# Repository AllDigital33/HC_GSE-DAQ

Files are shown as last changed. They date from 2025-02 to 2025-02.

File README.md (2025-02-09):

# HalfCat Custom GSE and DAQ

See attached overview PDF for details

WHY BUILD A HALFCAT CUSTOM GSE?  
  
The commercial GSE controller design that is detailed in the HalfCat HCR-5100 Mojave Sphinx guidebook works well. It is battle tested with a combined 50+ static fires and launches. It is infinitely easier and cheaper to setup than building your own GSE Controller or DAQ system. HalfCat has always been optimized for low cost, ease and accessibility, and is a great entry point to learn liquid rocketry. 
  
We built our custom HalfCat GSE and DAQ only because we had built ten previous versions for other liquid rockets. It only required minor edits to our existing PCBs, software, and iPad remote. Also, our overall “RocketTalk” project includes a full featured flight computer talking to our hand-held base, as well as the GSE, so we have one integrated hand-held remote talking across three radios to the pad and the rocket. This allows us to fill, launch, and track the rocket all in one, although the GSE Controller and code is separate and can be isolated, especially when doing static fires or testing not involving flight.
  
That said, if you have an amateur EE and some code junkies on your team and you want your own custom GSE controller or DAQ then our open sourced solution can provide you with some good ideas and a starting point. We intentionally built everything with the amateur maker in mind – including Arduino source code, EasyEDA schematics and PCB design, and Apple iOS Swift code. Building your own GSE controller could also be a fun upgrade for a team that has already built and launched their first Mojave Sphinx. 
  
As an added disclaimer… Our HC GSE Controller was developed/modified over the course of 8-10 weeks to support our Mojave Sphinx build, but it is still very much a WIP. We’ve decided to take a snapshot and share our learnings, so student groups can learn, borrow, or reuse some of our ideas and our sloppy code. 
  
FULLY INTEGRATED WITH HALFCAT MOJAVE SPHINX GSE PLUMBING  
  
It should be noted that we used the exact same servos, valves, plumbing, and fittings as specified in HCR 5100 for the Mojave Sphinx GSE. The only addition in our setup is the custom GSE Controller with radio remote and a permanently mounted pressure transducer on the rocket tank (connected back through the umbilical). 
  
GSE CONTROLLER FEATURES  
  
• Control of two pad servo valves for N2O fill and CO2 purging.  
• Control of rocket N2O and fuel main valves  
• Monitoring/recording of rocket tank PT  
• Monitoring/recording of chamber PT (static fire)  
• Igniter firing and local continuity check  
• Full featured three channel DAQ recorder for static fire analysis (tank PT, chamber PT, load cell)  
• Hazard power safety key  
• Automated process tasks for loading and launching to ensure exact timing  
  
iPAD TOUCH REMOTE FEATURES  
  
• Two tab-based control screens including:  
• Main GSE Screen:  
&nbsp;&nbsp;• Manual valve and igniter control  
&nbsp;&nbsp;• Automated processes (launch and load)  
&nbsp;&nbsp;• DAQ control  
&nbsp;&nbsp;• Arming & Disarming  
• GSE Configuration Screen:  
&nbsp;&nbsp;• Launch/Static fire mode  
&nbsp;&nbsp;• Set servo stops  
&nbsp;&nbsp;• Zero PTs  
&nbsp;&nbsp;• Set PT ranges  
   
TECHNOLOGY SUMMARY  
-------------------------------  
  
GSE Controller
  
• Teensy 4.1 Arm7 Microcontroller  
• SD card for DAQ and command logging  
• Arduino IDE / Single C++ Sketch  
• NiceRF LoRa 611Pro 433Mhz serial TTY radio (or use 900 Mhz)  
• Uses 12.6v Lipo battery  
• ADS1115 four channel 16bit ADC  
• DB9 connectors for rocket umbilical  
• DB9 connectors for pad valves  
• 6 pin avionics connector for chamber PT and load cell amplifier (separate)  
• CPU heatsink strapping for thermal management  
• Custom PCB developed using EasyEDA and printed through JLCPCB  
  
iPad Touch-based Remote  
  
• Standard iPad mini (wifi only)  
• Uses RedSerial cable to interface with NiceRF LoRa radio  
• -or- Custom Bluetooth bridge using an ESP32 connected to a NiceRF LoRa 611Pro 433Mhz serial radio  
• Apple xCode IDE with iOS Swift code  
• 7.2v lipo battery and iPad battery  

DISCLAIMER

The open-source code and hardware designs ("Materials") provided here are related to the development and launching of bipropellant liquid rockets. The authors and contributors of these Materials provide them for educational and informational purposes only. The authors and contributors disclaim all responsibility for any injuries, damages, or losses of any nature whatsoever, whether direct, indirect, punitive, incidental, special, consequential, or any other damages, to persons or property, arising out of or connected with the use, misuse, or inability to use the Materials provided here.

Mike & Preston
Sinnoh Sphinx+ SN05
@RocketTalk33 in the Discord

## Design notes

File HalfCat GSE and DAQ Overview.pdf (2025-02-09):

# HalfCat Custom GSE Controller & DAQ

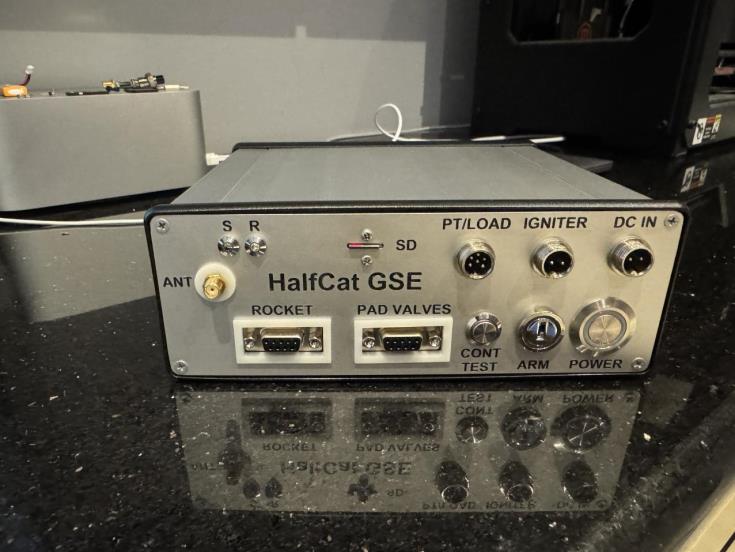
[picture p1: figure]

# Overview and Design

# Version 1.0 – February 2025 Mike & Preston Brinker

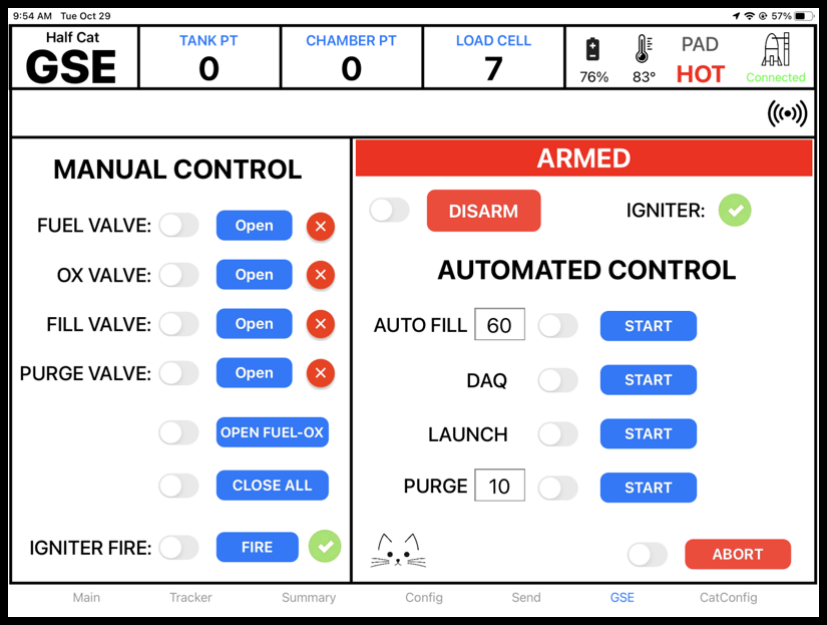
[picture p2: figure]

# Why build a GSE controller for HalfCat Rockets?

The commercial GSE controller design that is detailed in the HalfCat HCR-5100 Mojave Sphinx guidebook works well. It is battle tested with a combined 50+ static fires and launches. It is infinitely easier and cheaper to setup than building your own GSE Controller or DAQ system. HalfCat has always been optimized for low cost, ease and accessibility, and is a great entry point to learn liquid rocketry.

We built our custom HalfCat GSE and DAQ only because we had built ten previous versions for other liquid rockets. It only required minor edits to our existing PCBs, software, and iPad remote. Also, our overall “RocketTalk” project includes a full featured flight computer talking to our hand-held base, as well as the GSE, so we have one integrated hand-held remote talking across three radios to the pad and the rocket. This allows us to fill, launch, and track the rocket all in one, although the GSE Controller and code is separate and can be isolated, especially when doing static fires or testing not involving flight.

That said, if you have an amateur EE and some code junkies on your team and you want your own custom GSE controller or DAQ then our open sourced solution can provide you with some good ideas and a starting point. We intentionally built everything with the amateur maker in mind – including Arduino source code, EasyEDA schematics and PCB design, and Apple iOS Swift code. Building your own GSE controller could also be a fun upgrade for a team that has already built and launched their first Mojave Sphinx.

As an added disclaimer… Our HC GSE Controller was developed/modified over the course of 8-10 weeks to support our Mojave Sphinx build, but it is still very much a WIP. We’ve decided to take a snapshot and share our learnings, so student groups can learn, borrow, or reuse some of our ideas and our sloppy code.

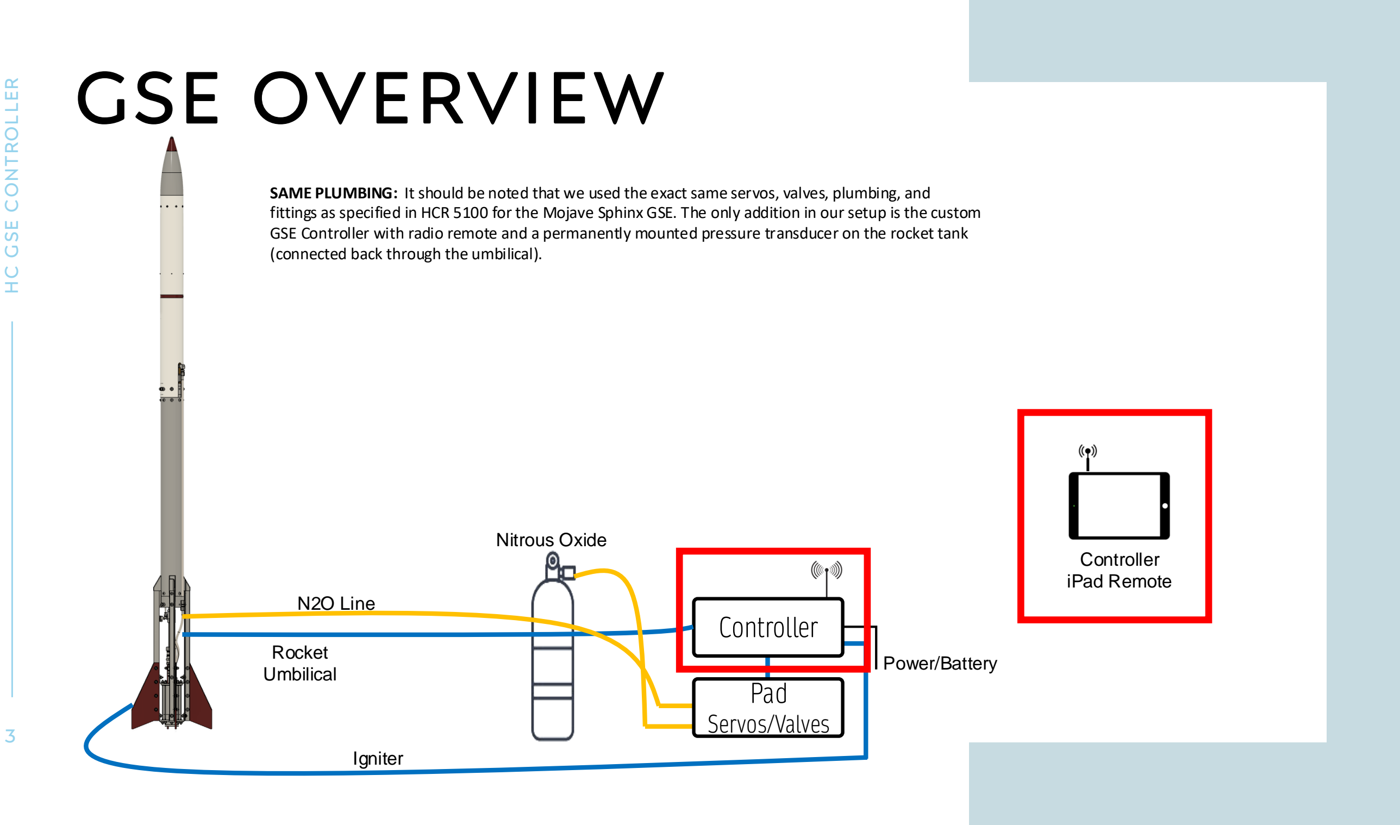
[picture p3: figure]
GSE OVERVIEW; 3HC GSE CONTROLLER; Pad Servos/Valves; Controller; Power/Battery Rocket Umbilical; N2O Line; Nitrous Oxide; Controller iPad Remote; Igniter; (connected back through the umbilical).

SAME PLUMBING: It should be noted that we used the exact same servos, valves, plumbing, and fittings as specified in HCR 5100 for the Mojave Sphinx GSE. The only addition in our setup is the custom GSE Controller with radio remote and a permanently mounted pressure transducer on the rocket tank

# OPEN GSE PROJECT

4HC GSE CONTROLLER

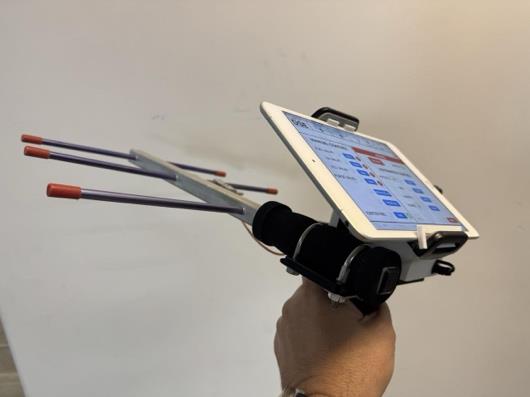
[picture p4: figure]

Below are the general design principles that drove the development of the controller and remote:

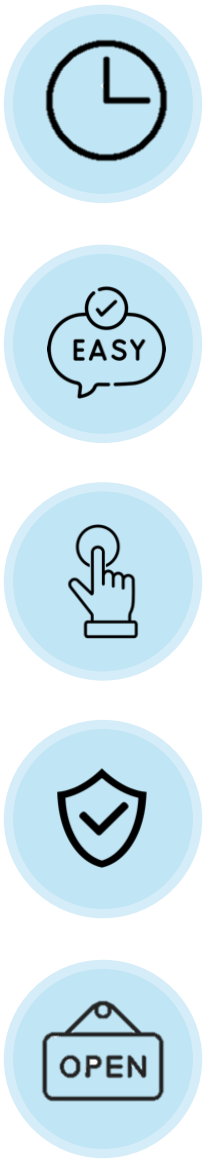
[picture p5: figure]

## 1. MINIMAL DESIGN – MAXIMUM FEATURES

Simplified and compact design with minimum features to load, pressurize, launch, and static fire a HalfCat rocket, integrating into the overall design of Mojave Sphinx.

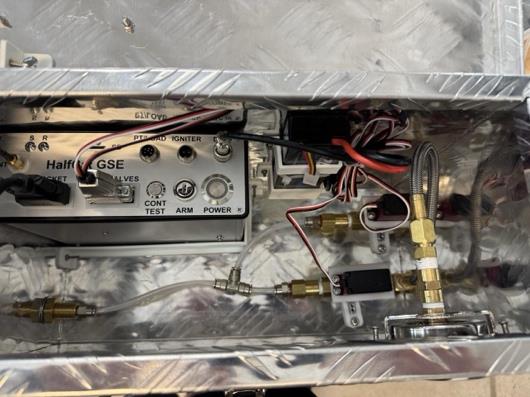
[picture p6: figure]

## 2. BASIC COMPONENTS AND IDE’S

## 3. SIMPLIFIED USER INTERFACE

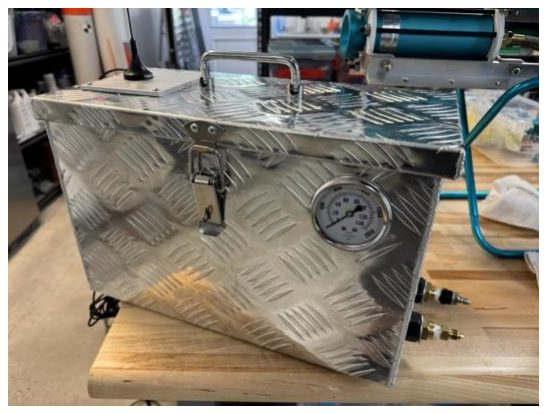
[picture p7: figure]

## 4. SAFETY AND ERROR SYSTEMS

## 5. OPEN SOURCE

### Developed using Arduino-based MCU (Teensy 4.1-Arm7), EasyEDA PCB layout, and an iPad

tablet remote (Apple xCode IDE w/Swift).

Custom remote provides simplified UI and error controls to minimize the human risks related to loading/pressurizing, and launching and DAQ data capture.

### Automated processes in the controller for loading and launch, over-current and fault

protections, error checking, and more.

Code and hardware design available to US University student teams.

### www.RocketTalk.net

# CONTROLLER SYSTEMS

## Rocket

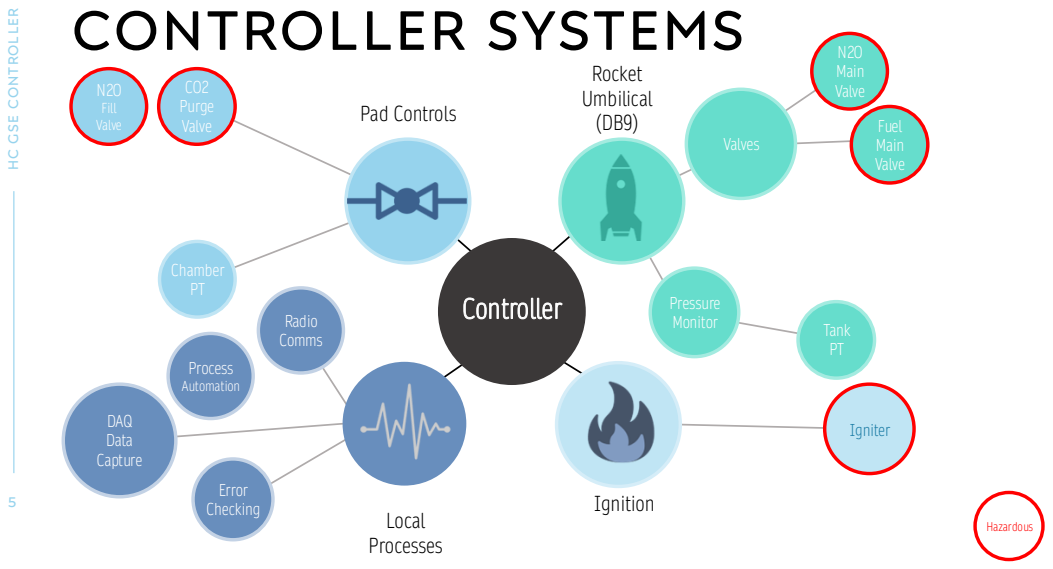
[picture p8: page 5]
5HC GSE CONTROLLER; Pad Controls; Umbilical (DB9); Controller; Ignition; Local Processes; DAQ Data Capture; Radio Comms; Igniter; N2O Main Valve; Valves; Pressure; Monitor; Tank; Error Checking; CO2 Purge; Valve; Fuel; Main Valve; N2O Fill Valve; Chamber PT; Hazardous; Process Automation

# SYSTEMS FEATURE SUMMARY

6OPEN GSE CONTROLLER

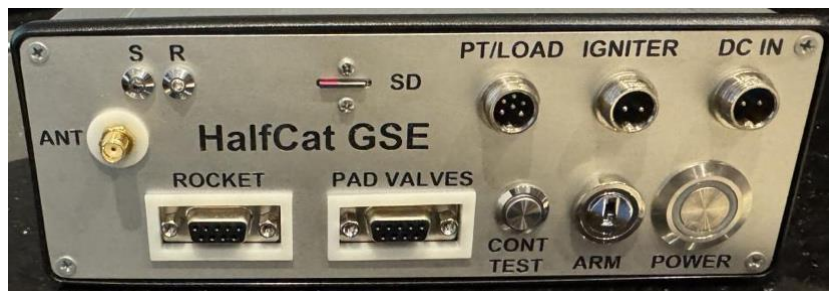
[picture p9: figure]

GSE Controller

- Control of two pad servo valves for N2O fill and CO2 purging.
- Control of rocket N2O and fuel main valves
- Monitoring/recording of rocket tank PT
- Monitoring/recording of chamber PT (static fire)
- Igniter firing and local continuity check
- Full featured three channel DAQ recorder for static fire analysis (tank PT, chamber PT, load cell)
- Hazard power safety key
- Automated process tasks for loading and launching to ensure exact timing

iPad Touch-based Remote

- Two tab-based control screens including:
- Main GSE Screen:
- Manual valve and igniter control
- Automated processes (launch and load)
- DAQ control
- Arming & Disarming
- GSE Configuration Screen:
- Launch/Static fire mode
- Set servo stops
- Zero PTs
- Set PT ranges

# TECHNOLOGY SUMMARY

7 OPEN GSE CONTROLLER

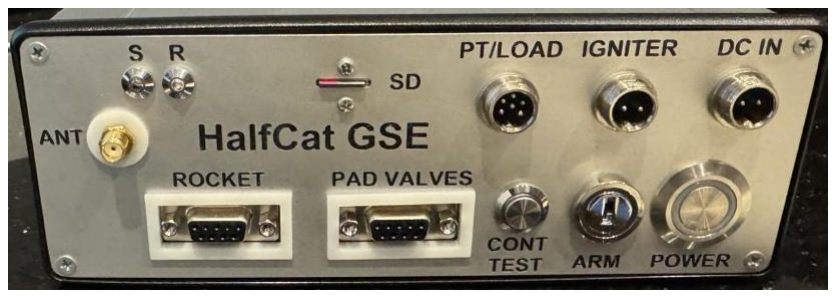
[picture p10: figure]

GSE Controller

- Teensy 4.1 Arm7 Microcontroller
- SD card for DAQ and command logging
- Arduino IDE / Single C++ Sketch
- NiceRF LoRa 611Pro 433Mhz serial TTY radio (or use 900 Mhz)
- Uses 12.6v Lipo battery
- ADS1115 four channel 16bit ADC
- DB9 connectors for rocket umbilical
- DB9 connectors for pad valves
- 6 pin avionics connector for chamber PT and load cell amplifier (separate)
- CPU heatsink strapping for thermal management
- Custom PCB developed using EasyEDA and printed through JLCPCB

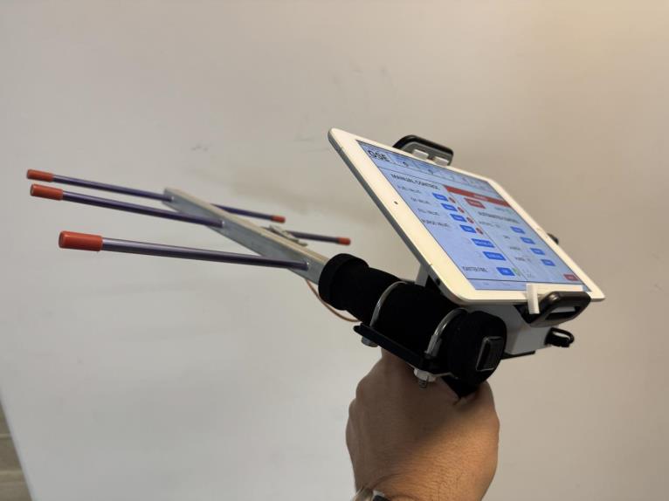
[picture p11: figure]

iPad Touch-based Remote

- Standard iPad mini (wifi only)
- Uses RedSerial cable to interface with NiceRF LoRa radio
- -or- Custom Bluetooth bridge using an ESP32 connected to a NiceRF LoRa 611Pro 433Mhz serial radio
- Apple xCode IDE with iOS Swift code
- 7.2v lipo battery and iPad battery

# HARDWARE – EXTERNAL I/O

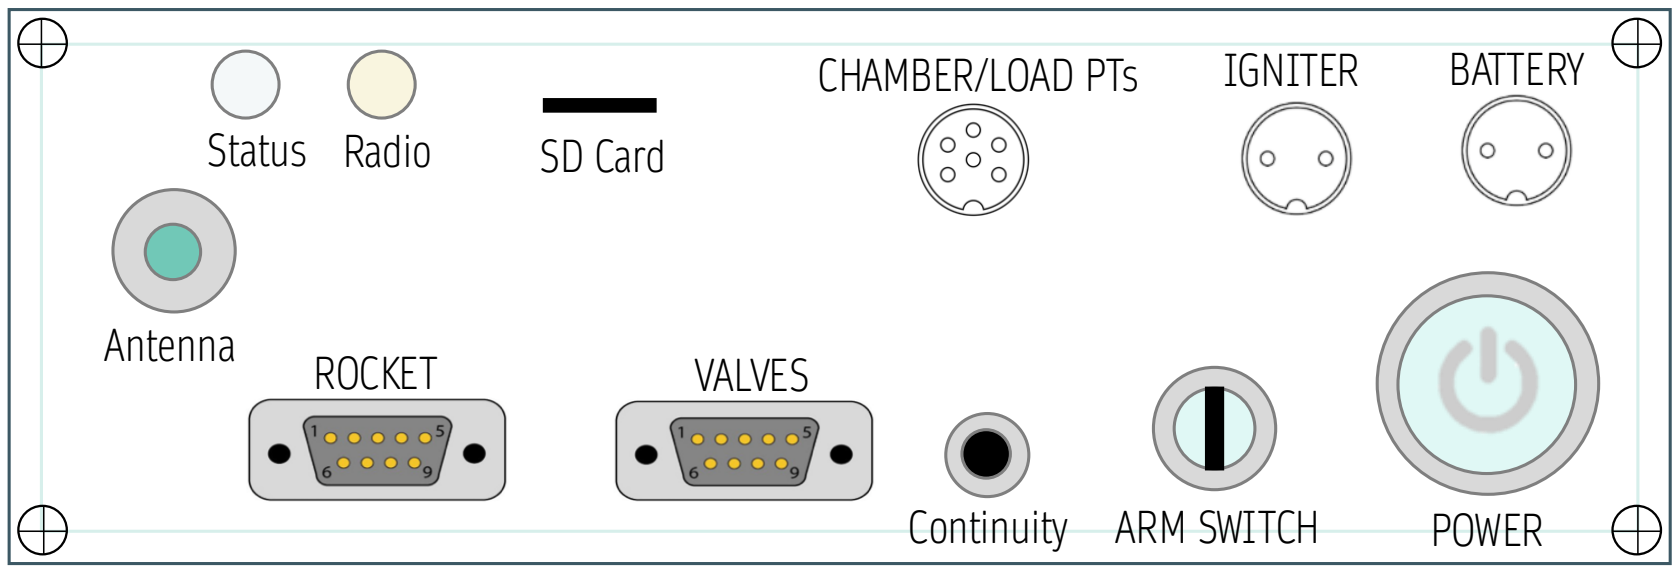
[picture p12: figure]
Antenna; Status; ROCKET; VALVES; ARM SWITCH; BATTERY; SD Card; Continuity; IGNITER; POWER; Radio; CHAMBER/LOAD PTs

# A word about servos

This was our first project controlling servos with an Arduino in a “rugged environment”. All of our past GSE controllers were directly powering solenoid valves with high current drivers or signaling using an ethernet bus. Servos use Pulse Width Modulation (PWM) to communicate between the MCU and the servo. The Teensy 4.1 has lots of examples and libraries, but ultimately there are variances and nuances with each servo that require you to set the stops for your preferred positions (like 0 and 90 degrees for opening/closing a valve).

The other issue you run into with servos is over-heating and burn-out, especially when working with quarter turn valves. When the MCU sends a command to the servo to move 90 degrees it will keep moving until its internal encoder says it has reached 90 degrees. So, if your hardware shifts a bit on the rocket and now when your valve is closed the servo is at 89 degrees, you will think the servo finished, but in reality it is sitting there quietly burning 2 amps and trying desperately to go another 1 degree. Eventually it will either burn-out or your battery will die. This is why servos are notorious for burning out.

So we store a configuration file and make it easy in the configuration UI to set the stops for each servo on each valve. We also use a solid state switch to turn on the servo power when we want to command it and then turn the power off two seconds later, preventing the servos from overheating or consuming battery. The servos do not need to stay energized once the valves have opened or closed. This protects them from over-heating or drawing too much power.

Also, we found that the servos operated about 20% fast at 6v vs. 5v, so our GSE is using a 6v regulator. Every millisecond counts when opening the main N2O and Fuel valves on the rocket, to make sure they are flowing well while the igniter cartridge is still burning. The extra voltage lowers the open/close time by about 30ms.

# GSE CONTROLLER DETAILS

# GSE Controller – Conceptual Architecture

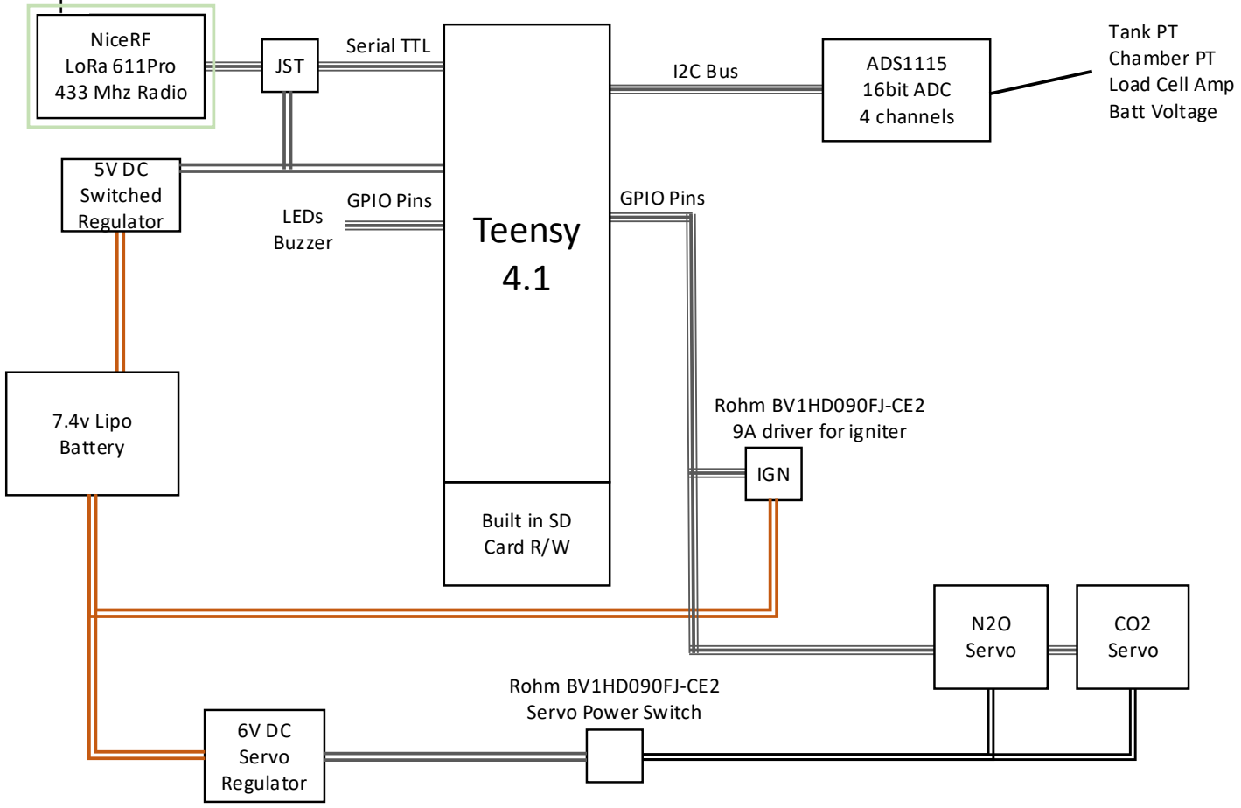
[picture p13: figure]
Teensy 4.1; ADS1115 16bit ADC 4 channels; Built in SD Card R/W; I2C Bus; NiceRF LoRa 611Pro 433 Mhz Radio; Serial TTL; 5V DC Switched Regulator; 7.4v Lipo Battery; 6V DC Servo Regulator; JST; GPIO Pins; IGN; Rohm BV1HD090FJ-CE2 9A driver for igniter; LEDs Buzzer; Rohm BV1HD090FJ-CE2 Servo Power Switch; N2O Servo; CO2 Servo; Tank PT Chamber PT Load Cell Amp Batt Voltage

External

Note: You can get same
modules in 915Mhz
certified

# Current Technology Choices – Controller PCB

- Teensy 4.1: The T4.1 with its Arm Cortex-M7 is just insanely fast for an MCU and it is loaded with a lot of versatile GPIO. The T4.1 also has a built-in SD card for easy data recording (used with an extender). The fast MCU allows us to sample four channels of data at 200Hz for static fire testing. We compile at a slower clock speed (384 Mhz) for cooler thermal performance.
- Radios: We have tried a number of different radios, but we are very happy with our NiceRF LoRa 611Pro radios on 433 Mhz (FCC amateur radio license required). You can get similar radios in 900 Mhz that don’t require a license. The Lora technology is great and is very reliable. Order TTY versions and use on serial I/O.
- ADS1115 16bit ADC: We use one four channel ADC. One channel is for the tank PT, one for the chamber PT, one connects to the load cell amplifier (separate circuit), and one monitors the battery voltage. The ADC operates over I2C.
- Igniter Driver - Rohm BV1HD090FJ-CE2: This is a single channel 8A high-side driver used for triggering the igniter. It also provides excellent over-current protection, but doesn’t shut-down when firing an igniter. It has a status pin that provides a safe continuity check.
- Servo Power Driver - Rohm BV1HD090FJ-CE2: We use another Rohm driver to switch the servo 6v power. Each time we move a servo to open or close a valve we energize it for two seconds and then de-energize it so there is no risk of overheating or damaging the servo.
- 5V Regulator: We use a Pololu 5v 2.5A switched regulators (D24V22F5) to power the Teensy, external PTs, and the Radio.
- 6V Regulator: We use a Pololu 6v 5.5A switched regulators (D36V50F6) to power the servos. Running the servos at 6V helps them operate close to their maximum speed.
- Reverse Polarity Protection: We use a P-Channel Mosfet (IRF9Z24PBF), along with a Zener diode (SZMMSZ5246BT1G) and 10K resistor to provide reverse polarity protection for the PCB.
- Other: We use Vishay VO1400AEFTR Optoisolated relays to report fuse status for the one fuse

# Controller Board – Custom PCB

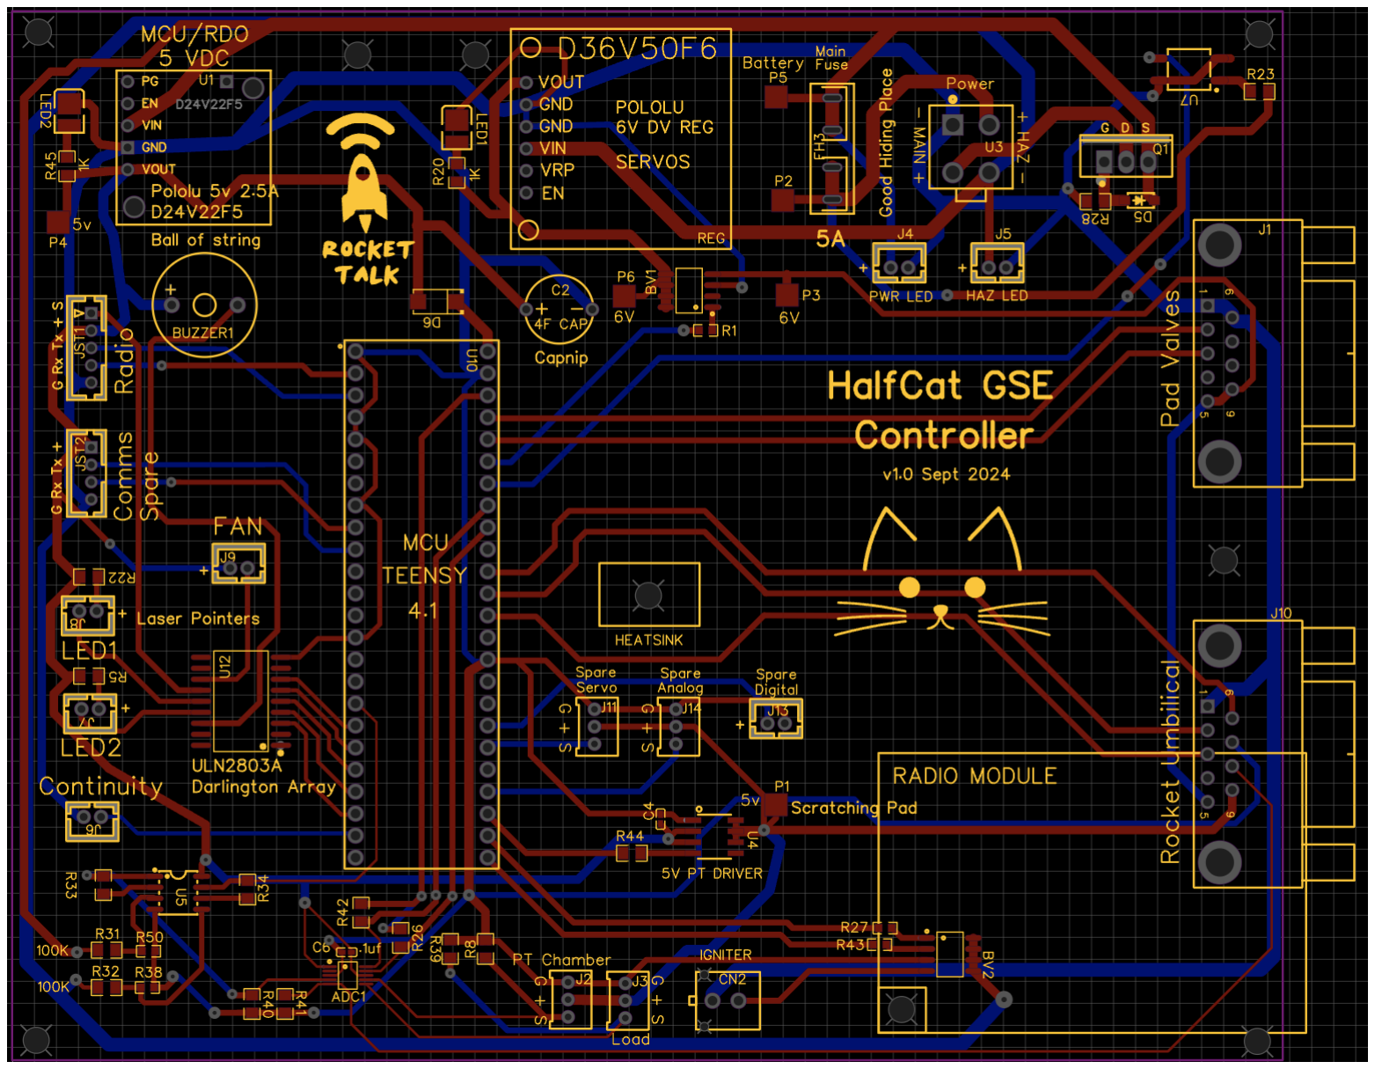
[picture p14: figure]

## The schematic and custom PCB are designed in EasyEDA and printed and ordered through JLCPCB (via EasyEDA). It

really is easy.

## The PCB is a two-layer board printed with

2oz traces for added current capacity.

# Controller Board – Custom PCB

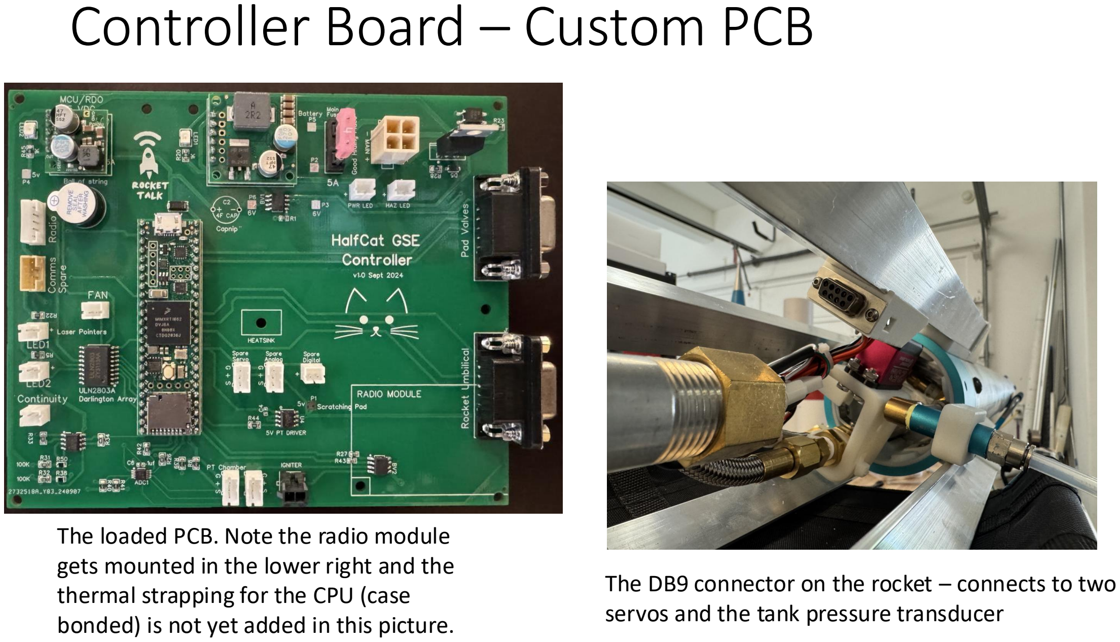
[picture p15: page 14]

## The loaded PCB. Note the radio module gets mounted in the lower right and the thermal strapping for the CPU (case

bonded) is not yet added in this picture.

## The DB9 connector on the rocket – connects to two servos and the tank pressure transducer

# Controller Board – Custom PCB

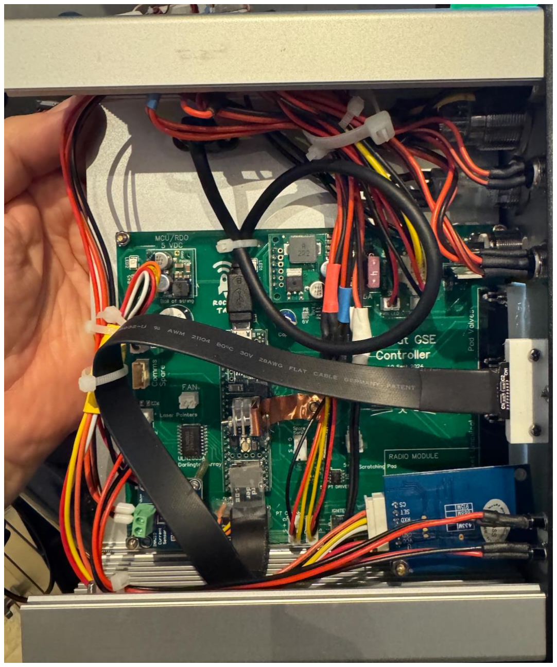
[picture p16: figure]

## Fully wired inside a Hammond aluminum box

## (p/n 1455U1601 - 160mmx191mm)

# Controller Board – Schematic

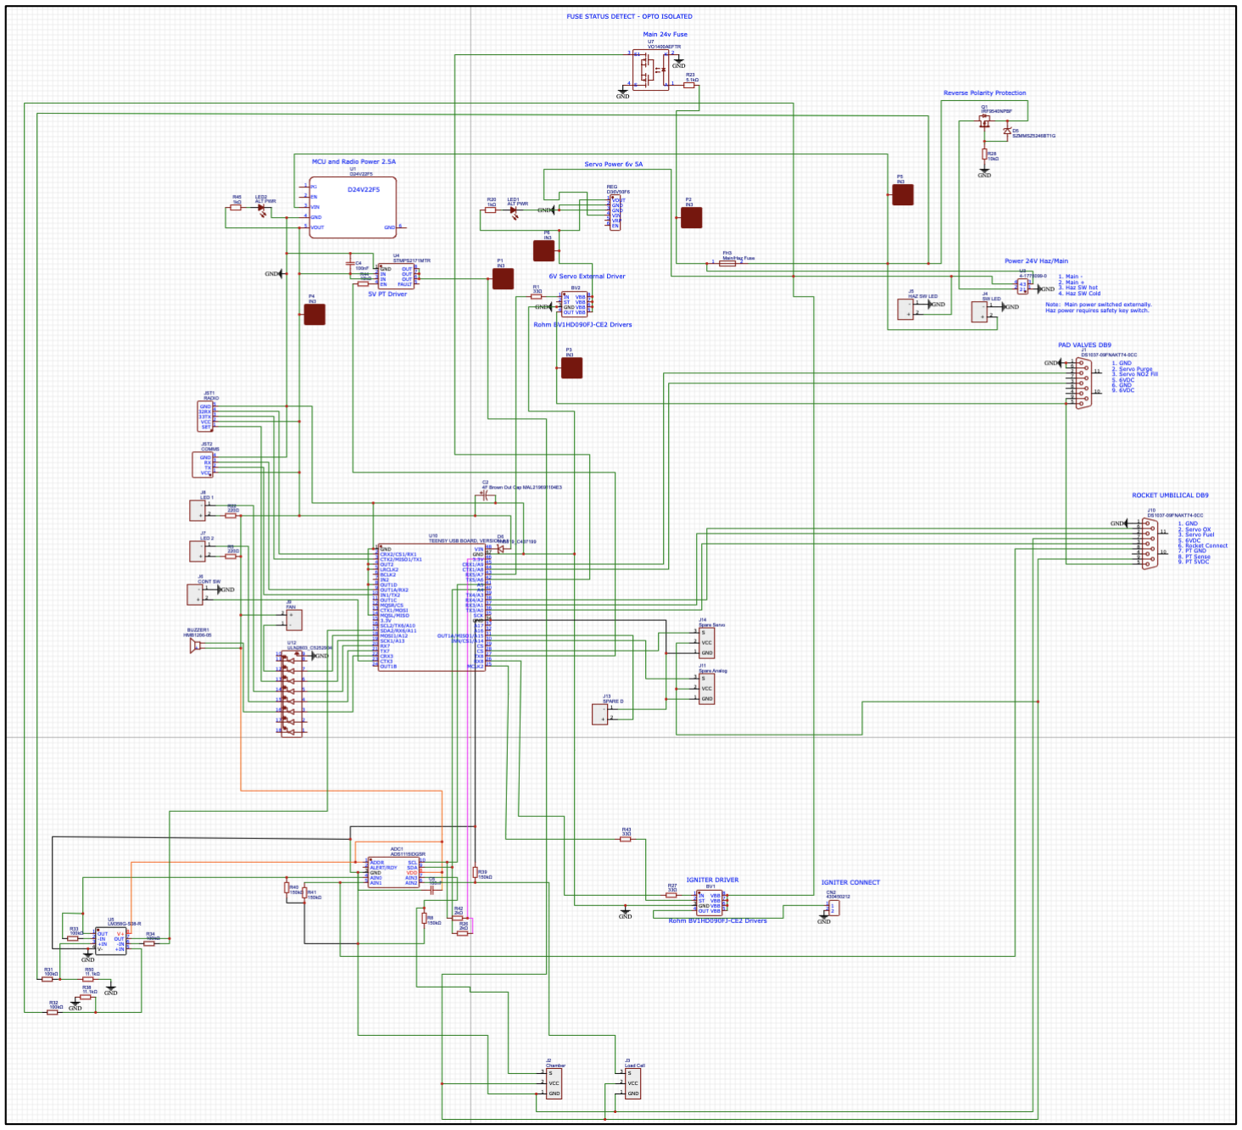
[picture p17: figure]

# Controller Board – Code Design

The Teensy code is built from a single C sketch in the Arduino (Teensyduino) IDE. It utilizes some external libraries for the ADCs and logging, but is otherwise self-contained in a single code file.

We used to use Teensy Threads to partition the code into three parts, but we’ve found the code is more reliable when run as a single sequential sketch and the Teensy processor is more than fast enough to sample and record at 100+ sps/Hz for DAQ logging.

Each of the activities in the main loop are throttled using timers, so the highest priority tasks, like sampling, process faster and more often. Here is the general order of operations:

### - Check radio (receive) - Check radio (send)

- Sample
- DAQ Record
- Housekeeping

### - Check Pressures (for alerts) - Fuse check - Rocket connected check - Igniter continuity check - Voltage check - Manual continuity test switch - Check automated processes - Error/Health check - Send full status to remote (every 5 sec)

# iPAD REMOTE

# iPad Remote – Conceptual Architecture

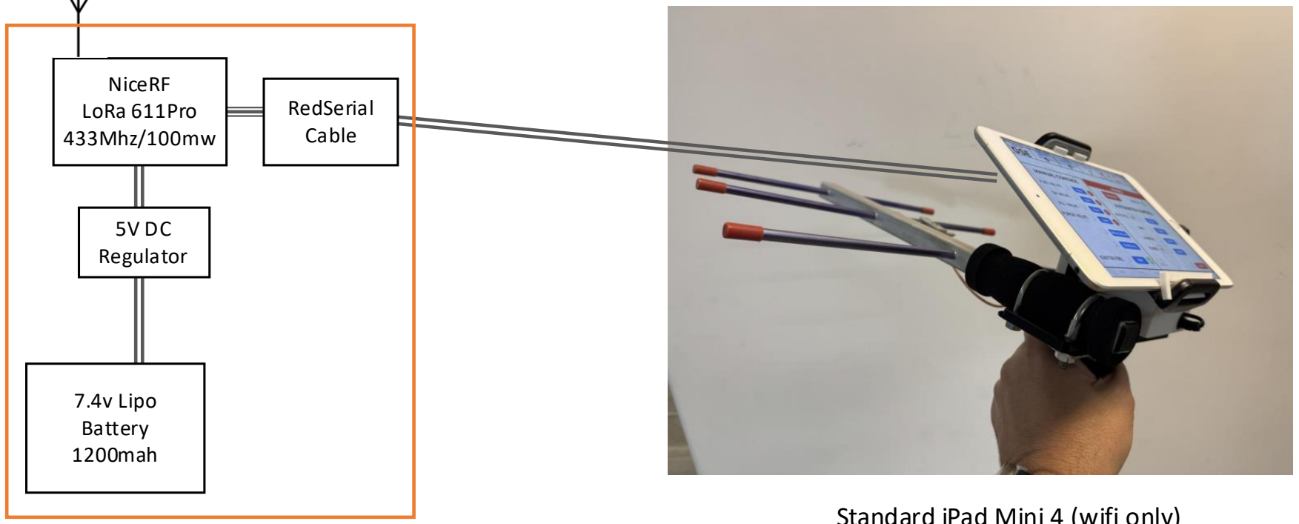
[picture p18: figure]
NiceRF LoRa 611Pro 433Mhz/100mw; 5V DC Regulator; 7.4v Lipo Battery 1200mah; RedSerial Cable

## This version is using a direct RedSerial cable

Standard iPad Mini 4 (wifi only)

# iPad Remote – Optional Bluetooth

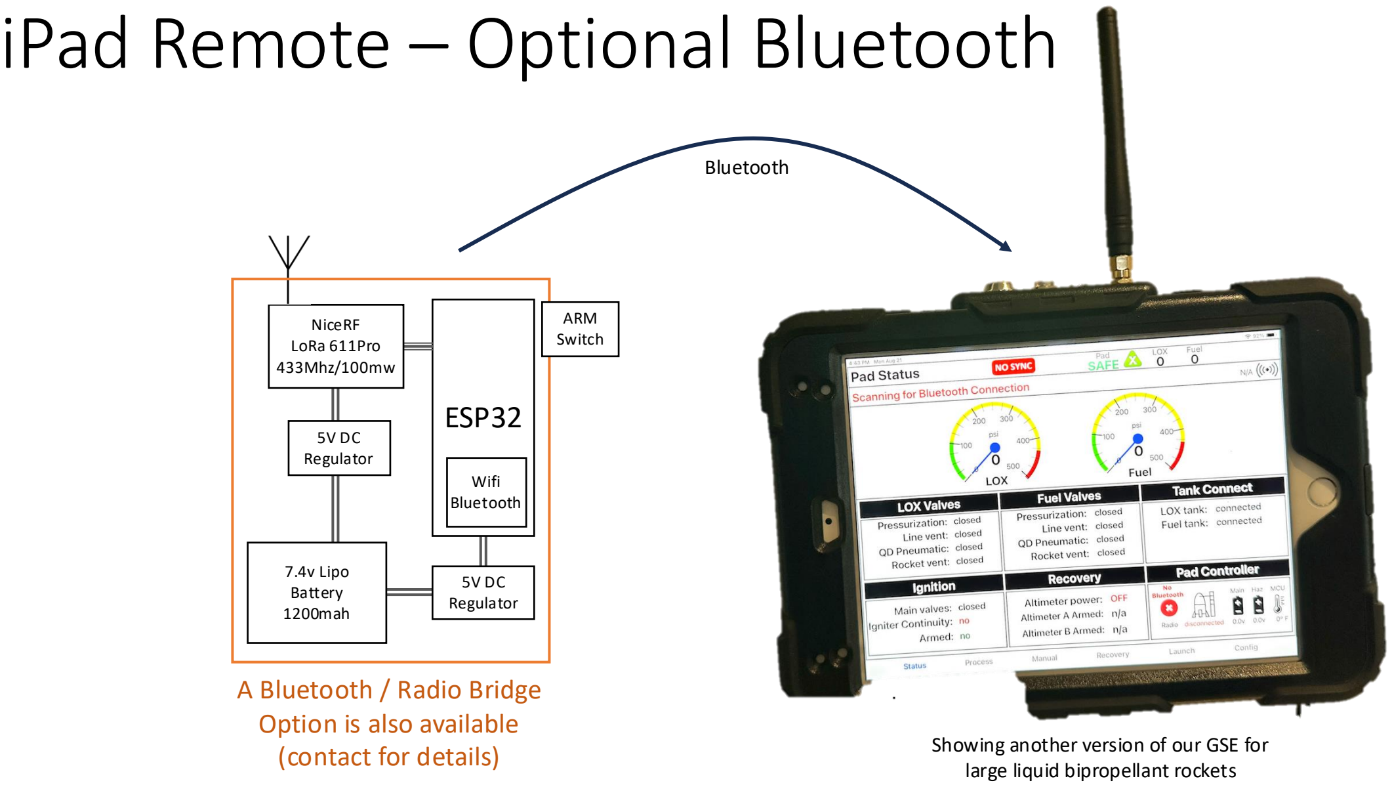
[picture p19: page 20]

## ESP32

NiceRF
LoRa 611Pro
433Mhz/100mw

5V DC
Regulator

7.4v Lipo
Battery
1200mah

## A Bluetooth / Radio Bridge Option is also available

(contact for details) | Showing another version of our GSE for large liquid bipropellant rockets

Wifi
Bluetooth

5V DC
Regulator

ARM
Switch

Bluetooth

# iPad Remote – Screens

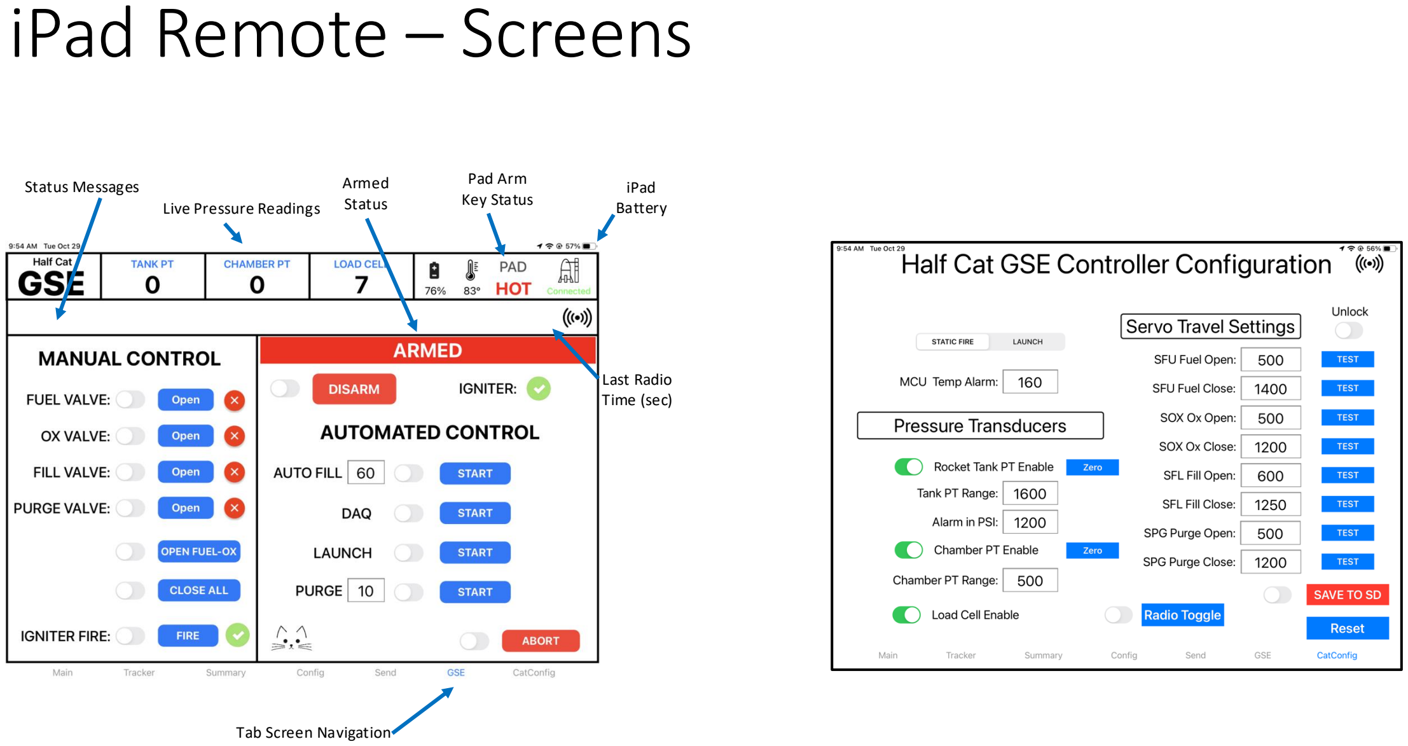
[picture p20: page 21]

Status Messages
Live Pressure Readings

Tab Screen Navigation

Pad Arm
Key Status

Armed
Status

Last Radio
Time (sec)

iPad
Battery

# Current Technology Choices – Remote

- iPad Mini: When we decided to develop the remote using a touch-based tablet we chose an Apple iPad mini, due to the ubiquity and longevity of the Apple product line. It also provides an extremely intuitive UI which was a major design principle. The iOS Swift IDE (in Apple’s xcode) is free and easy to learn, but to fully exploit Apple’s development environment a $100/year developer fee is required.
- Bluetooth Bridge Option: Our original designs used a proprietary cable (Redpark) to connect the iPad to the serial TTY LoRa radio, but it is proprietary and difficult to get. The Redpark cable also was not Apple sanctioned and their primary solution was to interface to the iPad using Bluetooth. So we built a small Bluetooth “bridge” from an ESP32 using a small Arduino sketch. The ESP32 receives data from the LoRa serial radio and then passes it to the iPad via Bluetooth. This has proven to be extremely reliable. It also gave us the ability to add a physical key switch to the iPad for Arming the controller.
- Battery with Bluetooth: EMEPOVGY 2S Lipo Battery Airsoft 1200mAh 7.4V 20C
- Other: Our first version of this solution used a full-size 9” iPad, but we found that an iPad Mini worked just fine. Using a project box from Polycase (VM-35MMTT ) provides a great one-handed solution. Also the iPad case from Seymac provides good protection in the rugged environment.

# Load Cell Amplifier

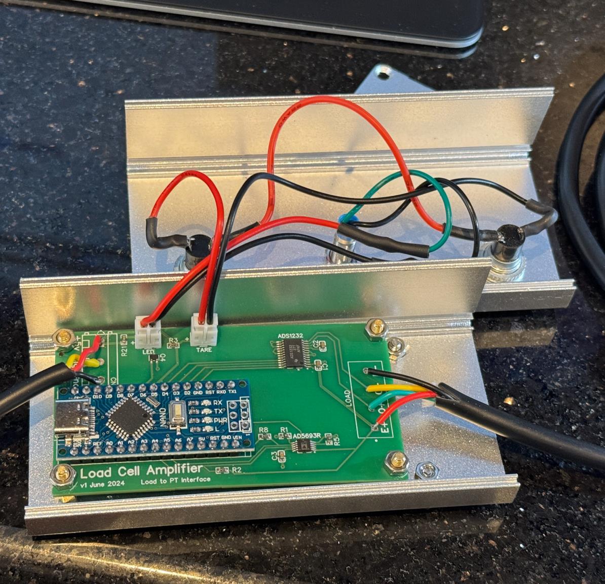
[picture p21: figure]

# LOAD CELL AMPLIFIER

## 24OPEN GSE CONTROLLER

A strain gauge load cell requires an amplifier, since the output is in tiny millivolts, so you will need to wire an amplifier close to the load cell (within 2-3 feet) and then run a higher voltage signal line back to your DAQ.

In our case, we made a custom amplifier circuit that will feed into our 5v ADC in the GSE Controller by sending 2.5v (2500mv) to the GSE when reading zero. It then increments one mv per pound for positive force and decrements one mv per pound for negative (hanging weight of the rocket/propellant). This allows us to better capture load taking into consideration the weight of the rocket and expending propellant over time. We log to SD 2500mv +/- 1mv for each pound of force.

It is built using an Arduino Nano and an ADS1232 ADC (connected to the strain gauge) and a AD5693R chip to send back the 0-5v signal to the controller.

# LOAD CELL AMPLIFIER

## 25OPEN GSE CONTROLLER

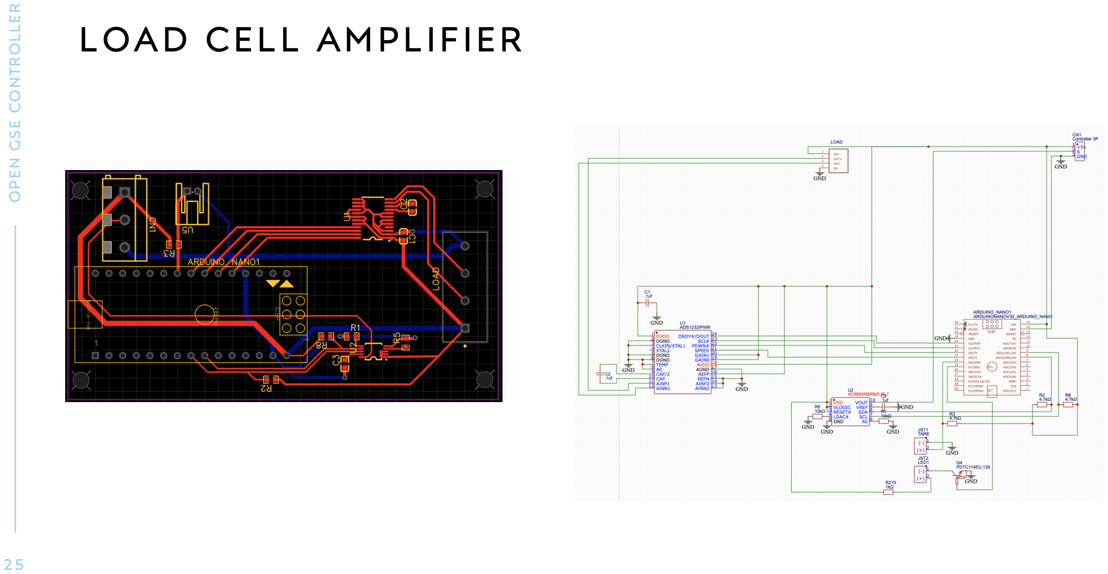
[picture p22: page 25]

# Disclaimer:

The open-source code and hardware designs ("Materials") provided here are related to the development and launching of bipropellant liquid rockets. The authors and contributors of these Materials provide them for educational and informational purposes only.

WARNING: LAUNCHING LIQUID ROCKETS IS AN INHERENTLY DANGEROUS ACTIVITY. The use of the Materials involves significant risks, including, but not limited to, serious physical injury, disability, and death. Anyone using, modifying, or distributing these Materials must understand and accept these risks. If you choose to use these Materials, you do so at your own risk.

The authors and contributors of these Materials make no representations or warranties of any kind, express or implied, about the completeness, accuracy, reliability, suitability, or availability with respect to the Materials. Any reliance you place on such information is therefore strictly at your own risk.

In no event will the authors or contributors be liable for any loss or damage including without limitation, indirect or consequential loss or damage, or any loss or damage whatsoever arising from loss of data or profits arising out of, or in connection with, the use of these Materials.

The authors and contributors disclaim all responsibility for any injuries, damages, or losses of any nature whatsoever, whether direct, indirect, punitive, incidental, special, consequential, or any other damages, to persons or property, arising out of or connected with the use, misuse, or inability to use the Materials provided here.

BY USING THESE MATERIALS, YOU ACKNOWLEDGE THAT YOU HAVE READ THIS DISCLAIMER, UNDERSTAND IT, AND AGREE TO BE BOUND BY IT.

# Questions?

# @PAD33space on Twitter/X @AllDigital on TRF info@rocketTalk.net

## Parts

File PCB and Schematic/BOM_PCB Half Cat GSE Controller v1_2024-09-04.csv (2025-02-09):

ID | Name | Designator | Footprint | Quantity | Manufacturer Part | Manufacturer | Supplier | Supplier Part | Price
1 | D24V22F5 | U1 | D24V22F5 | 1
2 | D36V50F6 | REG | D36V50F6 | 1
3 | Spare Analog | J11 | PH-3A | 1 | B3B-PH-K-S(LF)(SN) | JST | LCSC | C131339 | 0.034
4 | SPARE D | J13 | CONN-TH_B2B-PH-K-S | 1 | B2B-PH-K-S(LF)(SN) | JST | LCSC | C131337 | 0.03
5 | Spare Servo | J14 | PH-3A | 1 | B3B-PH-K-S(LF)(SN) | JST | LCSC | C131339 | 0.034
6 | BV2 | BV1 | SOP-8_L4.9-W3.9-P1.27-LS6.0-BL | 1 | BV1HD090FJ-CE2 | ROHM(罗姆) | LCSC | C2150182 | 2.737
7 | ADS1115IDGSR | ADC1 | MSOP-10_L3.0-W3.0-P0.50-LS5.0-BL | 1 | ADS1115IDGSR | TI(德州仪器) | LCSC | C37593 | 1.044
8 | HMB1206-05 | BUZZER1 | BUZ-TH_BD12.0-P7.60-D0.6-FD | 1 | HMB1206-05 | HNDZ | LCSC | C96095 | 0.265
9 | BV1 | BV2 | SOP-8_L4.9-W3.9-P1.27-LS6.0-BL | 1 | BV1HD090FJ-CE2 | ROHM(罗姆) | LCSC | C2150182 | 2.737
10 | 4F Brown Out Cap MAL219691104E3 | C2 | CAP_ROUND_7.5MM | 1
11 | 100nF | C4,C6 | C0402 | 2 | GRM155B31C104KA87D | muRata(村田) | LCSC | C85951 | 0.003
12 | 430450212 | CN2 | CONN-TH_430450212 | 1 | 430450212 | MOLEX | LCSC | C293362 | 0.367
13 | SZMMSZ5246BT1G | D5 | SOD-123_L2.7-W1.6-LS3.7-RD-1 | 1 | SZMMSZ5246BT1G | onsemi(安森美) | LCSC | C513075 | 0.093
14 | 1N5819_C437199 | D6 | SMA_L4.4-W2.6-LS5.0-RD | 1 | 1N5819 | KEXIN(科信) | LCSC | C437199 | 0.017
15 | Main/Haz Fuse | FH3 | LITTLEFUSE 01000063Z | 1 | 01000063Z | Littlefuse | LCSC | 01000063Z
16 | DS1037-09FNAKT74-0CC | J1,J10 | DSUB-TH_DS1037-09FNAKT74-0CC | 2 | DS1037-09FNAKT74-0CC | CONNFLY | LCSC | C75749 | 0.301
17 | Chamber | J2 | PH-3A | 1 | B3B-PH-K-S(LF)(SN) | JST | LCSC | C131339 | 0.034
18 | Load Cell | J3 | PH-3A | 1 | B3B-PH-K-S(LF)(SN) | JST | LCSC | C131339 | 0.034
19 | SW LED | J4 | CONN-TH_B2B-PH-K-S | 1 | B2B-PH-K-S(LF)(SN) | JST | LCSC | C131337 | 0.03
20 | HAZ SW LED | J5 | CONN-TH_B2B-PH-K-S | 1 | B2B-PH-K-S(LF)(SN) | JST | LCSC | C131337 | 0.03
21 | CONT SW | J6 | CONN-TH_B2B-PH-K-S | 1 | B2B-PH-K-S(LF)(SN) | JST | LCSC | C131337 | 0.03
22 | LED 2 | J7 | CONN-TH_B2B-PH-K-S | 1 | B2B-PH-K-S(LF)(SN) | JST | LCSC | C131337 | 0.03
23 | LED 1 | J8 | CONN-TH_B2B-PH-K-S | 1 | B2B-PH-K-S(LF)(SN) | JST | LCSC | C131337 | 0.03
24 | FAN | J9 | CONN-TH_B2B-PH-K-S | 1 | B2B-PH-K-S(LF)(SN) | JST | LCSC | C131337 | 0.03
25 | RADIO | JST1 | CONN-TH_B5B-PH-K-S-LF-SN | 1 | B5B-PH-K-S(LF)(SN) | JST | LCSC | C157993 | 0.038
26 | COMMS | JST2 | CONN-TH_B4B-PH-K-LF-SN | 1 | B4B-PH-K(LF)(SN) | JST | LCSC | C265289 | 0.076
27 | ALT PWR | LED1,LED2 | LED-SMD_L3.5-W2.8-R-RD | 2 | 67-21/R6C-FN2Q1BZ/2T | EVERLIGHT | LCSC | C74350 | 0.066
28 | IN3 | P1,P2,P3,P4,P5,P6 | PAD_1.5X2.5 | 6 | Soldering pad |  |  | undefined
29 | IRF9540NPBF | Q1 | TO-220-3_L10.0-W4.5-P2.54-L | 1 | IRF9540NPBF | Infineon(英飞凌) | LCSC | C2575 | 0.409
30 | 33Ω | R1,R27,R43 | R0603 | 3 | RM06FTN33R0 | 大毅科技 | LCSC | C188015 | 0.001
31 | 11.1kΩ | R38,R50 | R0603 | 2 | RT0603BRD0711K1L | YAGEO(国巨) | LCSC | C5197511 | 0.024
32 | 220Ω | R5,R22 | R0805 | 2 | MCWR08X221 JTL | Multicomp | LCSC | C243171 | 0.004
33 | 150kΩ | R8,R39,R40,R41 | R0805 | 4 | RK73B2ATTD154J | KOA | LCSC | C276119 | 0.005
34 | 1kΩ | R20,R45 | R0805 | 2 | TC0550F1001T5J | UNI-ROYAL(厚声) | LCSC | C517536 | 0.008
35 | 5.1kΩ | R23 | R0805 | 1 | SCR0805F5K1 | VO(翔胜) | LCSC | C3016714 | 0.002
36 | 2kΩ | R26,R42 | R0805 | 2 | RC0805DR-072KL | YAGEO(国巨) | LCSC | C164147 | 0.014
37 | 10kΩ | R28,R44 | R0805 | 2 | HPCR0805F10K0K9 | RESI(开步睿思) | LCSC | C365230 | 0.004
38 | 100kΩ | R31,R32,R33,R34 | R0805 | 4 | RM10JTN104 | 大毅科技 | LCSC | C153167 | 0.002
39 | 4-1775099-0 | U3 | CONN-TH_4P-P4.20_TE_4-1775099-0 | 1 | 4-1775099-0 | TE Connectivity(美国泰科) | LCSC | C5164039 | 0.453
40 | STMPS2171MTR | U4 | SO-8_L4.9-W3.9-P1.27-LS6.0-BL | 1 | STMPS2171MTR | ST(意法半导体) | LCSC | C2150330 | 0.493
41 | LM358G-S08-R | U5 | SOIC-8_L5.0-W4.0-P1.27-LS6.0-BL | 1 | LM358G-S08-R | UTC | LCSC | C71101 | 0.059
42 | VO1400AEFTR | U7 | SOP-4_L4.6-W4.4-P2.54-LS7.0-TL | 1 | VO1400AEFTR | VISHAY(威世) | LCSC | C142551 | 1.037
43 | TEENSY USB BOARD, VERSION 4.1 | U10 | COMM-TH_L61.0-W17.8-P2.54 | 1 | Teensy USB Board, Version 4.1 | null | LCSC | C9900060513
44 | ULN2803_C5252904 | U12 | SOP-18_L11.5-W7.5-P1.27-LS10.3-BL | 1 | ULN2803 | MSKSEMI(美森科) | LCSC | C5252904 | 0.187

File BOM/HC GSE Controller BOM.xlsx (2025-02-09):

 | Half Cat Custom GSE Controller and DAQ
 | BOM
 | version 1 - 2/2/2025
 | GSE CONTROLLER (ESTIMATED TBD)
 | QTY | Part Number | Description | Unit Price | Tax | Shipping | Ex Total Price | Min Purchase | Source | Notes | Link
 | MAIN BOX
 | 1 | 1455U1601 | Hammond Box 190m x 160m x 66mm | 35.94 | 2.70 | 9.00 | 47.64 |  | Mouser |  | https://www.mouser.com/ProductDetail/Hammond-Manufacturing/1455U1601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
 | 1 |  | Custom top plate machined | 35.00 | 2.62 | 10.00 | 47.62 |  | JLC3D
 | 1 |  | Power Switch uxcell Latching Metal Push Button Switch 22mm | 14.49 | 1.09 | 0.00 | 15.58 |  | Amazon |  | https://a.co/d/ifg8pvQ
 | 1 |  | Continuity Switch - Momentary Push Button Switch 12mm | 4.00 | 0.30 | 0.00 | 4.30 | yes | Amazon | Order prewired pk of 6 | https://a.co/d/6r6VOOG
 | 1 |  | Arm key switch - 16mm red 3-6v | 2.56 | 0.19 | 1.99 | 4.74 |  | AliExpress |  | https://www.aliexpress.us/item/3256803859396303.html
 | 1 | Lora611pro | Radio 915 MHz - NiceRF Lora611pro 100mw | 16.00 | 1.20 | 0.00 | 17.20 |  | AliExpress / NiceRF | Confirm FCC certified version | https://www.aliexpress.us/item/3256806011499899.html
 | 1 |  | Power conn: ATX 2 pin | 7.49 | 0.56 | 0.00 | 8.05 | yes | Amazon |  | https://a.co/d/dR5XRIx
 | 1 |  | LED mounts x 2 | 3.00 | 0.22 | 0.00 | 3.23 | yes | Amazon |  | https://a.co/d/6YWw2OK
 | 2 |  | LEDs 3mm x 2 (green, red) | 1.00 | 0.07 | 0.00 | 2.15 | yes | Amazon | https://a.co/d/hwglX05 | https://a.co/d/59Hs2r3
 | 1 |  | 3D Printed DB connecter groms | 1.00 | 0.07 | 1.00 | 2.08 |  | JLC3D
 | 1 |  | 3D Printed antenna groms | 1.00 | 0.07 | 2.00 | 3.08 |  | JLC3D
 | 1 | ADA3258 | Panel Mount Extension USB Cable | 8.86 | 0.66 | 0.00 | 9.52 | yes | Amazon |  | https://a.co/d/0o2t8Ip
 | 1 |  | SD Card extender B33SH, 25cm | 10.13 | 0.76 | 3.66 | 14.55 |  | AliExpress |  | https://www.aliexpress.us/item/3256804330908697.html
 | 1 |  | Stand off 10mm x 3mm (female male) | 3.00 | 0.22 | 0.00 | 3.23 | yes | Amazon | stand-off kit | https://a.co/d/fuNCLa0
 | CUSTOM PCB
E | 1 |  | PCB and pre-assembled (partially) - Estimated to include all res, caps, DA, diodes, DB cons, ADCs, JSTs, led, optos | 60.00 | 4.50 | 4.00 | 68.50 |  | JLCPCB | Estimate
 | 2 |  | 5v 5A Polulu regulators | 27.95 | 2.10 | 4.00 | 68.09 |  | Polulu |  | https://www.pololu.com/product/2851
 | 1 |  | Teensy 4.1 with pins | 35.00 | 0.00 | 12.95 | 47.95 |  | Proto Supplies |  | https://protosupplies.com/product/teensy-4-1-fully-loaded/
 | 2 |  | BV1HD090FJ-CE2 | 2.20 | 0.17 | 0.22 | 5.17 |  | DigiKey |  | https://www.digikey.com/en/products/detail/rohm-semiconductor/BV1HD090FJ-CE2/10249266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
 | 3 |  | VO1400AEFTR | 1.09 | 0.08 | 0.11 | 3.84 |  | DigiKey | SSR Relay for fuse detect | https://www.digikey.com/en/products/detail/vishay-semiconductor-opto-division/VO1400AEFTR/4073970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
 | 1 |  | ADC: ADS1115BQDGSRQ1 | 6.35 | 0.48 | 0.64 | 7.46 |  | DigiKey |  | https://www.digikey.com/en/products/detail/texas-instruments/ADS1115BQDGSRQ1/6575621
 | 1 | MAL219691104E3 | 4F Capacitor | 10.74 | 0.81 | 1.07 | 12.62 |  | DigiKey |  | https://www.digikey.com/en/products/detail/vishay-beyschlag-draloric-bc-components/MAL219691104E3/5017510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
 | 1 | 3544-2 | PCB Fuse Blocks | 0.78 | 0.06 | 0.08 | 0.92 |  | DigiKey |  | https://www.digikey.com/en/products/detail/keystone-electronics/3544-2/316029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
 | 1 | 029707.5WXNV | 7A fuses FUSE AUTO 7.5A 32VDC BLADE MINI | 0.32 | 0.02 | 0.03 | 0.38 |  | DigiKey |  | https://www.digikey.com/en/products/detail/littelfuse-inc/029707-5WXNV/146586
 | 1 |  | Heatsink uxcell 7x7x6mm Black Thermal Self Adhesive | 4.00 | 0.30 | 0.00 | 4.30 | yes | Amazon |  | https://a.co/d/8giv6k3
 | 1 | 430450212 | Igniter: Molex Microfit 2P | 0.97 | 0.07 | 0.10 | 1.14 |  | DigiKey |  | https://www.digikey.com/en/products/detail/molex/0430450212/252502?s=N4IgTCBcDaIAwBYDMiCscwEYIF0C%2BQA
 | 1 | 4-1775099-0 | Power connector: 4 pin ATX connector (PC power 9A) | 0.30 | 0.02 | 0.03 | 0.35 |  | DigiKey |  | https://www.digikey.com/en/products/detail/te-connectivity-amp-connectors/4-1775099-0/5272721
 | 1
 | 1
 | 1
 | TOOLS AND CONSUMABLES
 | 1 |  | Zip ties 3mm x 100mm
 | 1 |  | Copper tape 2" | 1.00 | 0.07 | 0.10 | 1.18
 | 1 |  | 20awg silicon wire | 5.00 | 0.38 | 0.50 | 5.88
 | 1 |  | Wire clips for wire management | 2.00 | 0.15 | 0.20 | 2.35
 | 1 |  | Heat shrink - various sizes | 6.99 | 0.52 | 0.00 | 7.51 | yes | Amazon |  | https://a.co/d/22ZGyPW
 |  |  |  | 308.16 | 20.49 | 51.67 | 420.59
 | PAD CABLES AND BOX |  | (no box hardware)
 | QTY | Part Number | Description | Unit Price | Tax | Shipping | Ex Total Price | Min Purchase | Source | Notes | Link
 | MAIN BOX
 | 1 |  | Antenna 915mhz mag mount | 5.00 | 0.38 | 0.00 | 5.38 |  | Amazon |  | https://a.co/d/5b89Azy
 | 1 |  | Antenna grommets | 2.00 |  |  |  |  | JLC3D
 | 1 |  | DB9 Straight cable | 15.00 | 1.12 | 1.50 | 17.62 |  | TBD
 | 1 |  | Igniter Cable - 18 Gauge 2 Conductor Electrical Wire 25' | 11.99 | 0.90 | 0.00 | 12.89 |  | Amazon |  | https://a.co/d/0pno9xZ
 | 1 |  | Clip Leads for Igniter 1.77" | 5.00 | 0.38 | 0.00 | 5.38 | yes |  |  | https://a.co/d/54TRCeZ
 |  |  |  | 38.99 | 2.77 | 1.50 | 41.26

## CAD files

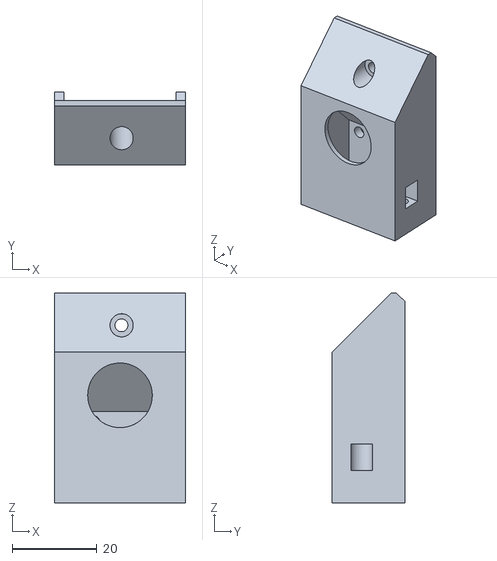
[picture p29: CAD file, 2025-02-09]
Machined and 3D/3D STL files/DB9 Rocket Umbilical Mount.stl
31.0 x 17.3 x 49.5

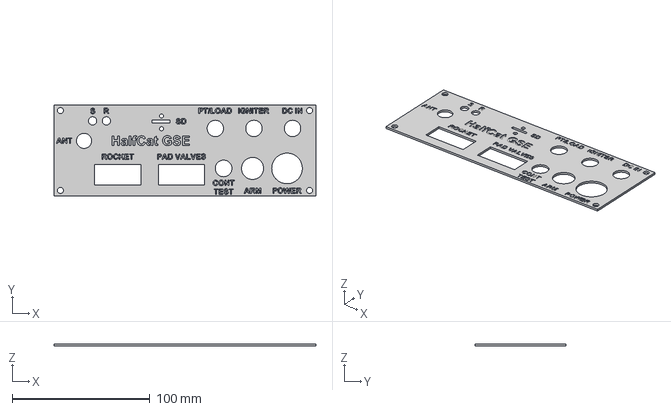
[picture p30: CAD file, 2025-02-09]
Machined and 3D/CNC/HC GSE Hammond Controller Top Panel.step
190.0 x 66.0 x 1.50 mm

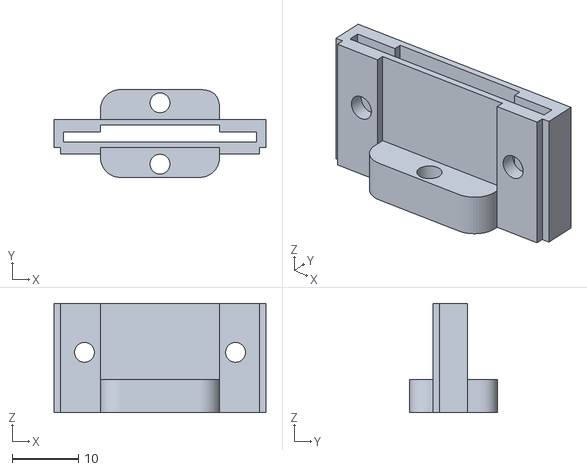
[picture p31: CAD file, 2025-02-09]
Machined and 3D/3D STL files/Controller SD card mount v1.stl
32.0 x 13.2 x 16.5

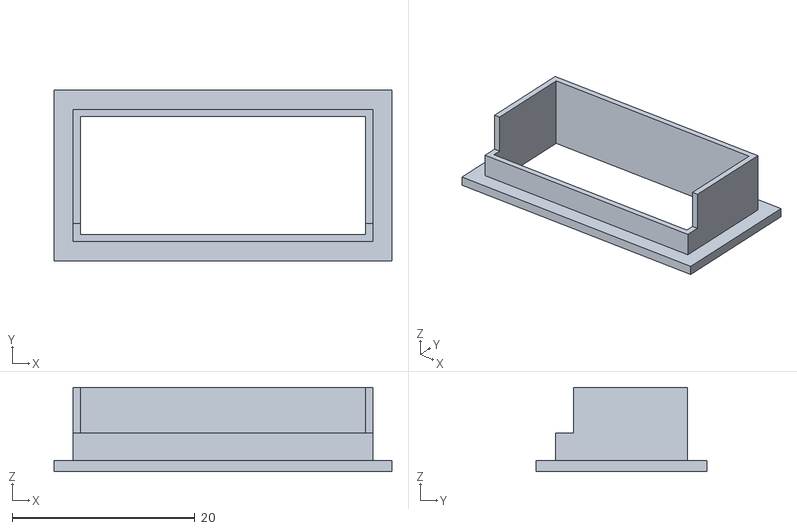
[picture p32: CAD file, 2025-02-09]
Machined and 3D/3D STL files/Controller-DB1-grommet.stl
37.0 x 18.7 x 9.20

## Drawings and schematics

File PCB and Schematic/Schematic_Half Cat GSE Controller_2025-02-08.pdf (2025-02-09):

## Power 24V Haz/Main

MCU and Radio Power 2.5A | Servo Power 6v 5A

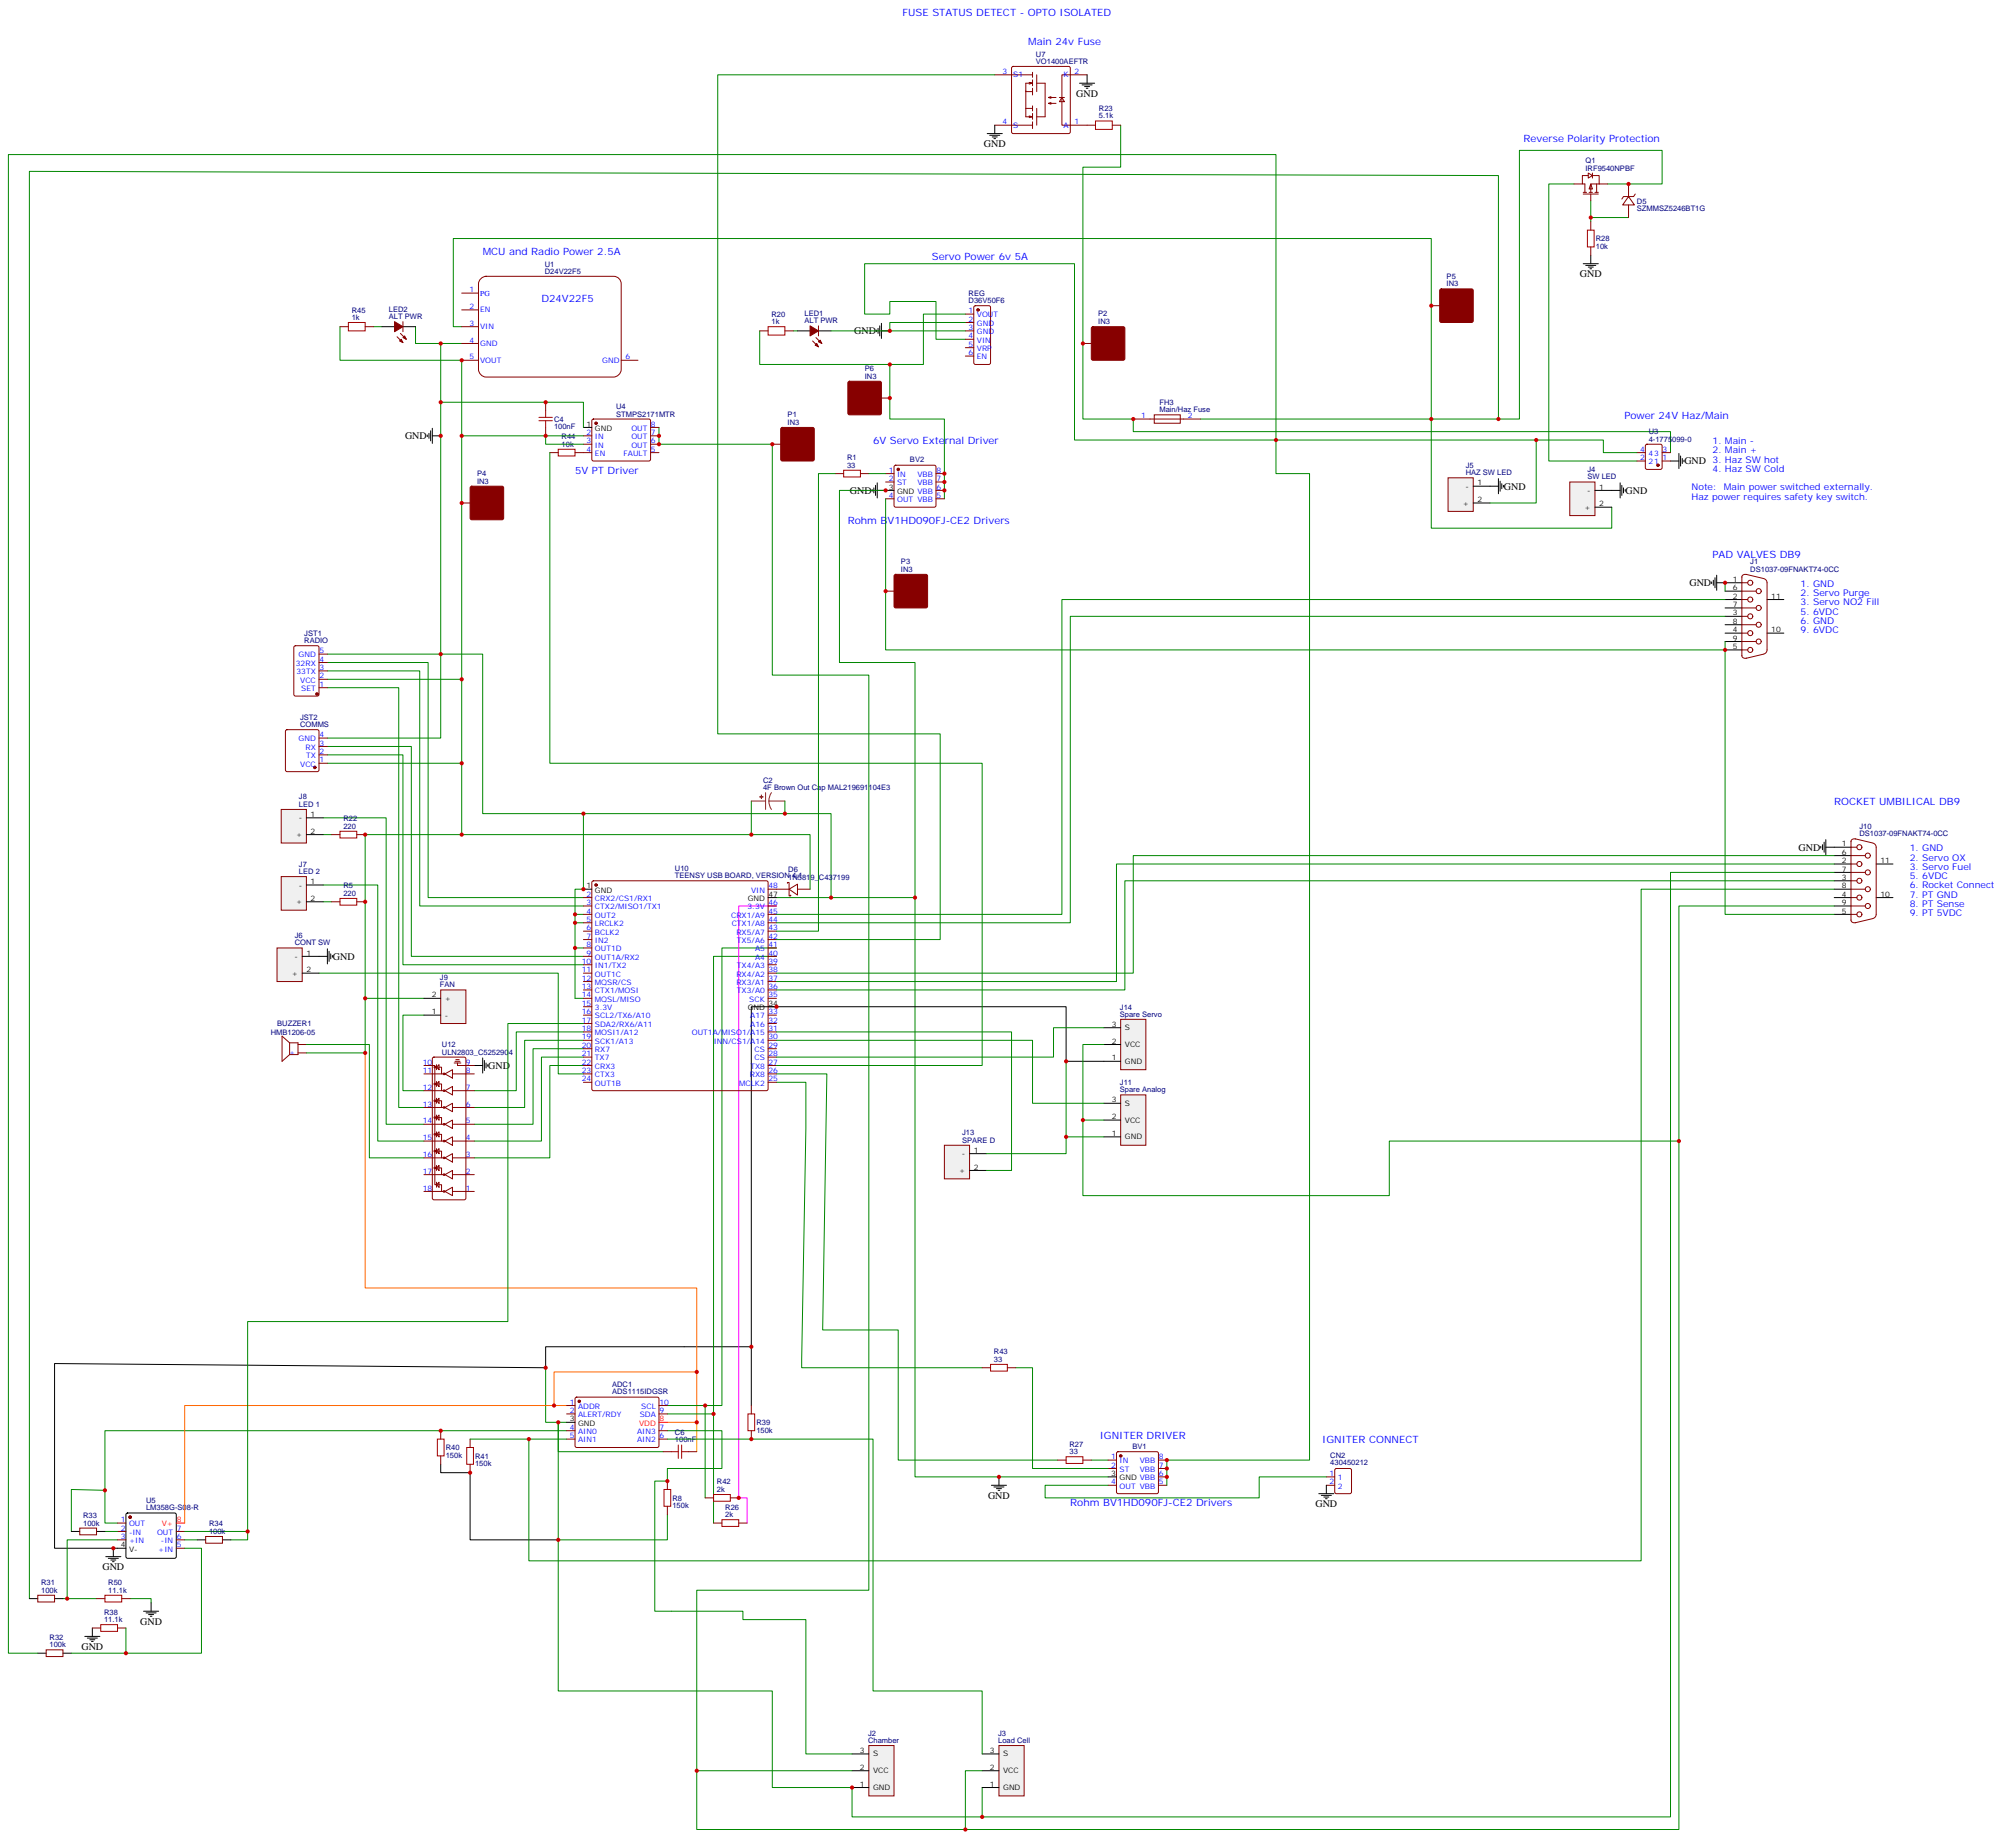
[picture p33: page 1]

FUSE STATUS DETECT - OPTO ISOLATED

TEENSY USB BOARD, VERSION 4.1

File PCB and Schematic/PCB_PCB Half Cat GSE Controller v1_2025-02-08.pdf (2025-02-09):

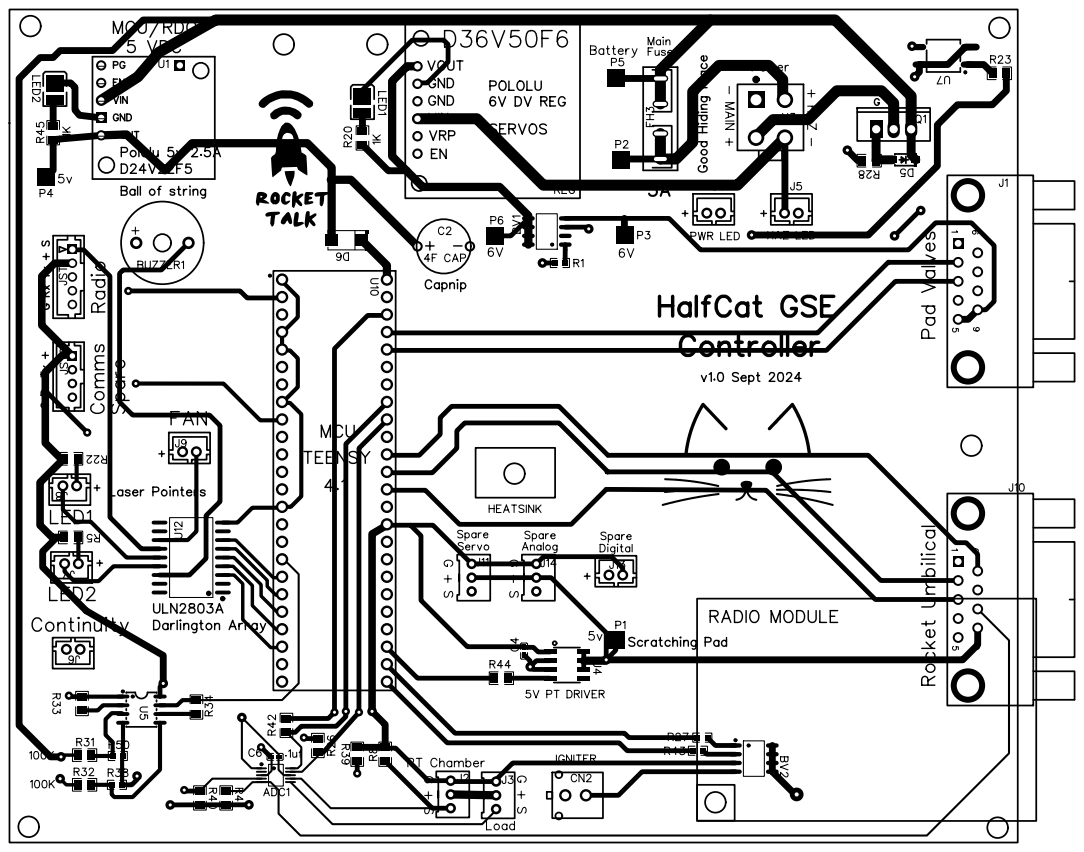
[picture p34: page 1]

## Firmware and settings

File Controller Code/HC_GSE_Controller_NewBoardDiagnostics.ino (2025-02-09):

/* Half Cat GSE Controller New Board Diagnostics
 *  
 *  Used to test all sensors, inputs and outputs on a new GSE Controller board
 *  Current hardware version is 1.0
 *  
 *   
 *  
 */ 

 // Pin configuration
  #define RXD1 0
  #define TXD1 1
  #define RXD2 7
  #define TXD2 8
  #define pin_rocketDetect 16 // PU 
  #define pin_igniterContinuity 33 
  #define pin_continuitySwitch 31 // PU
  #define pin_led1 28 //
  #define pin_led2 29 //
  #define pin_buzzer 30 //
  #define pin_igniterFIRE 34 // 
  #define pin_servoFill 22 
  #define pin_servoPurge 23
  #define pin_servoFuel 15
  #define pin_servoOx 14
  #define pin_servoSpare 36
  #define pin_hazVolts A11
  #define pin_radioSet 27
  #define pin_internalLED 13
  #define pin_ext5v 35
  #define pin_ext6v 21
  #define pin_fuseMain 20
  #define pin_fan 26
  #define pin_analogSpare A14
  #define pin_digSpare 39



  #include "Arduino.h"
  #include "ADS1115-Driver.h"
    extern "C" uint32_t set_arm_clock(uint32_t frequency); // required to set MCU clock speed
  ADS1115 ads1115a = ADS1115(0x49);


  #include <Wire.h>
  #include <Adafruit_INA219.h>
  Adafruit_INA219 ina219;

 //Servos
  #include <Servo.h> 
  Servo fuelServo;  
  Servo oxServo;
  Servo fillServo;
  Servo purgeServo;

 //Radio
 char theWord[100];
 int newWord = 0;

// For the flash memory
  //Little FS flash
  #include <LittleFS.h>
  char buf[512] = "";
  char fname1[32] = "/testfile.txt"; //testfile.txt
  //LittleFS_QSPIFlash myfs; // RT5.1
  LittleFS_QPINAND myfs; // used for fully loaded T4.1 W25N02KVZEIR
 
  File file, file1, file3;
//  #include <LittleFS_NAND.h>
  #include <stdarg.h>
  uint64_t fTot, totSize1;
  
  #include <TimeLib.h>  // for logging time


// Temperature from CPU
  extern float tempmonGetTemp(void);  

// just for SD
  #include "SD.h"
  #include <SPI.h> 
  File tempFile;

// enabling ADC channels

  bool aEnabled[8] = {1,1,1,1,1,1,1,1};
  

//************************************************************************************************************************************************************  SETUP
//************************************************************************************************************************************************************  SETUP

 
void setup() {

// Pin setup
  pinMode(pin_led1, OUTPUT);  digitalWrite(pin_led1, LOW);
  pinMode(pin_led2, OUTPUT);  digitalWrite(pin_led2, LOW);
  pinMode(pin_buzzer, OUTPUT);  digitalWrite(pin_buzzer, LOW);
  pinMode(pin_igniterFIRE, OUTPUT);  digitalWrite(pin_igniterFIRE, LOW);
  pinMode(pin_hazVolts, INPUT);

  pinMode(pin_igniterContinuity, INPUT_PULLUP);   
  pinMode(pin_rocketDetect, INPUT_PULLUP);  
  pinMode(pin_continuitySwitch, INPUT_PULLUP);  
  pinMode(pin_fuseMain, INPUT_PULLUP);

  pinMode(pin_radioSet, OUTPUT);digitalWrite(pin_radioSet, LOW);
  pinMode(pin_internalLED, OUTPUT); digitalWrite(pin_internalLED, LOW);
  pinMode(pin_ext5v, OUTPUT);digitalWrite(pin_ext5v, LOW);
  pinMode(pin_ext6v, OUTPUT);digitalWrite(pin_ext6v, LOW);
  pinMode(pin_fan, OUTPUT);digitalWrite(pin_fan, LOW);
  pinMode(pin_digSpare, OUTPUT);digitalWrite(pin_digSpare, LOW);

  fuelServo.attach(pin_servoFuel); 
  oxServo.attach(pin_servoOx);
  purgeServo.attach(pin_servoPurge);
  fillServo.attach(pin_servoFill);
  
  delay(4000);
  Serial.begin(115200);
  delay(100);
  Serial.println("Half Cat GSE New Board Diagnostics and Health Check");
  Serial.println(" ");Serial.println(" ");

  printCommands();

}

//************************************************************************************************************************************************************  MAIN LOOP
//************************************************************************************************************************************************************  MAIN LOOP

void loop() {

  char chIn = 255;
  if ( Serial.available() ) {
    do {
     if ( chIn != '0' && chIn != '1' && chIn != '2' && chIn != 'F' && chIn != '$' && chIn != 'C' && chIn != '#' && chIn != '3' && chIn != '4' && chIn != '5' && chIn != '6' && chIn != '7' && chIn != '8' && chIn != '9' && chIn != 'a' && chIn != 'b' && chIn != 'c' && chIn != 'd' && chIn != 'e' && chIn != 'f' && chIn != 'g' && chIn != 'h' && chIn != 'i' && chIn != 'j' && chIn != 'k' && chIn != 'l' && chIn != 'm' && chIn != 'n' && chIn != 'o' && chIn != 'p' && chIn != 'q' && chIn != 'r' && chIn != 's' && chIn != 't'&& chIn != 'u'&& chIn != 'v'&& chIn != 'w'&& chIn != 'x'&& chIn != 'y'&& chIn != 'z' && chIn != '?' && chIn != '!' && chIn != '&' && chIn != '*' && chIn != '+'  )
        chIn = Serial.read();
      else
        Serial.read();
    }
    while ( Serial.available() );
  }

  switch(chIn) {
    case '1':
      toggleLed1(); printCommands(); break;
    case '2':
      toggleLed2(); printCommands(); break;
    case '3':
      //toggleLed3(); printCommands(); break;                
    case '4':
      toggleLB(); printCommands(); break;
    case '5':
      toggle5v();printCommands(); break;
    case '6':
      toggle6v();printCommands(); break;
    case '7':
      checkCont();printCommands(); break;
    case '8':
      toggleIgniter(); printCommands(); break;
    case '9':
      RadioTXtest();printCommands(); break;
    case '0':
      toggleRset(); printCommands(); break;

      
    case 'a':
      servoFuelOpen();  printCommands(); break;
    case 'b':
      servoFuelClose(); printCommands(); break;
    case 'c':
      servoOxOpen(); printCommands(); break;
    case 'd':
      servoOxClose(); printCommands(); break;
    case 'e':
      servoFillOpen(); printCommands(); break;
    case 'f':
      servoFillClose(); printCommands(); break;
    case 'g':
      servoPurgeOpen(); printCommands(); break;
    case 'h':
      servoPurgeClose(); printCommands(); break;
    case 'i':
      rocketConnect(); printCommands(); break;
    case 'j':
      continuitySwitch(); printCommands(); break;
    case 'k':
      bothValves(); printCommands(); break;
    case 'l':
      //toggleV3(); printCommands(); break;
    case 'm':
     // toggleV4(); printCommands(); break;
    case 'n':
      showCurrent(); printCommands(); break;
    case 'o':
      //toggleV6(); printCommands(); break;
    case 'p':
      formatFlash(); printCommands(); break;
    case 'q':
      eraseFlash(); printCommands(); break;
    case 'r':
      printDirectory(); printCommands(); break;
    case 's':
      copy2SD(); printCommands(); break;
    case 't':
      flashLogging(); printCommands(); break;
    case 'u':
      //toggleValve("VPP"); printCommands(); break;
    case 'v':
      checkTemp(); printCommands(); break;
    case 'w':
      //toggleValve("VBO"); printCommands(); break;
    case 'x':
      I2Cscan(); printCommands(); break;
    case 'y':
      PTloop(); printCommands(); break;
    case 'z':
      //radioRead();printCommands(); break; //Configuration report
      radioTest();printCommands(); break;
    case '$':
      readConfig();printCommands(); break;
    case '#':
      readFile();printCommands(); break;
    case '?':
      toggleBuzzer(); printCommands(); break;
    case '&':
      toggleFan();printCommands(); break;
    case '*':
      fuseTest();printCommands(); break;
    case '+':
      checkVoltage();printCommands(); break;
    case 'C':
      DAQtest();printCommands(); break;
    case 'F':
      formatUnused();printCommands(); break;
  }
  
}

void printCommands() {
  Serial.println("  ");
  Serial.println("----------------------------------------------------------------------------------------------------------------------------------------------------------");
  Serial.println("COMMANDS:");
  Serial.println("      Local:  1-LED1, 2-LED2, 4-LED BLTIN, ?-Buzzer, 5-5vExt, 6-6v Ext, &-Fan ");
  Serial.println("    Sensing:  v-CPU Temp, j-Cont Switch, *-Fuses, +-Voltage n-Current");
  Serial.println("     Servos:  a-Fuel Open, b-Fuel Close, c-Ox Open, d-Ox Close, e-Fill Open, f-Fill Close, g-Purge Open, h-Purge close, k-both open");
  Serial.println("     Ignite:  7-Ign Continuity, 8-Igniter Fire"); 
  Serial.println("        PTs:  x-I2C Scan, y-PT values");
  Serial.println("      Radio:  z-Radio Test, 0-radio set, 9-Radio TX");
  Serial.println("         SD:  q-Quick Erase, r-Directory, t-Flash Logging Test, $-read config file, #-read file, C-DAQTest");  
  Serial.println("-----------------------------------------------------------------------------------------------------------------------------------------------------------");  
  Serial.println("  ");
}

void showCurrent() {

  Serial.println("INA219 Current Sensing");
  Serial.println(" ");
  if (! ina219.begin()) {
    Serial.println("Failed to find INA219 chip");
    return;
  }
  float shuntvoltage = 0;
  float busvoltage = 0;
  float current_mA = 0;
  float loadvoltage = 0;
  float power_mW = 0;

  shuntvoltage = ina219.getShuntVoltage_mV();
  busvoltage = ina219.getBusVoltage_V();
  current_mA = ina219.getCurrent_mA();
  power_mW = ina219.getPower_mW();
  loadvoltage = busvoltage + (shuntvoltage / 1000);
  
  Serial.print("Bus Voltage:   "); Serial.print(busvoltage); Serial.println(" V");
  Serial.print("Shunt Voltage: "); Serial.print(shuntvoltage); Serial.println(" mV");
  Serial.print("Load Voltage:  "); Serial.print(loadvoltage); Serial.println(" V");
  Serial.print("Current:       "); Serial.print(current_mA); Serial.println(" mA");
  Serial.print("Power:         "); Serial.print(power_mW); Serial.println(" mW");
  Serial.println("");



}



void servoFuelOpen() {

  Serial.println("Fuel Valve Open");
  Serial.println(" ");
  fuelServo.writeMicroseconds(500); // zero is open

}

void servoFuelClose() {

  Serial.println("Fuel Valve Close");
  Serial.println(" ");
  fuelServo.writeMicroseconds(1200); // 1200 is closed

}

void servoOxOpen() {

  Serial.println("Ox Valve Open");
  Serial.println(" ");
  oxServo.writeMicroseconds(500); // zero is open

}

void servoOxClose() {

  Serial.println("Ox Valve Close");
  Serial.println(" ");
  oxServo.writeMicroseconds(1200); // 1200 is closed

}


void bothValves() {

  Serial.println("Fill and Purge Valve Open Same time");
  Serial.println(" ");
  fillServo.writeMicroseconds(500); // zero is open
  purgeServo.writeMicroseconds(600); // zero is open





}




void servoFillOpen() {

  Serial.println("Fill Valve Open");
  Serial.println(" ");
  fillServo.writeMicroseconds(500); // zero is open

}

void servoFillClose() {

  Serial.println("Fill Valve Close");
  Serial.println(" ");
  fillServo.writeMicroseconds(1200); // 1200 is closed

}

void servoPurgeOpen() {

  Serial.println("Purge Valve Open");
  Serial.println(" ");
  purgeServo.writeMicroseconds(600); // zero is open

}

void servoPurgeClose() {

  Serial.println("Purge Valve Close");
  Serial.println(" ");
  purgeServo.writeMicroseconds(1200); // 1200 is closed

}

void checkVoltage() {

  Serial.println("Checking voltage using the ADC... 10s read 10s");
  Serial.println(" ");
  // ADS1115 
  Wire.begin();
  delay(1);
  ads1115a.reset();
  delay(100);

  ads1115a.setDeviceMode(ADS1115_MODE_SINGLE);
  ads1115a.setDataRate(ADS1115_DR_860_SPS);
  ads1115a.setPga(ADS1115_PGA_6_144);
  delay(100);

  Wire.setClock(400000); 
  
  delay(10000);

// ----------------------------------  Check Main Voltage  ------------------------
      elapsedMicros adcTimer = 0;
      float valueADC = 0.0;
      ads1115a.setMultiplexer(ADS1115_MUX_AIN0_GND);
      ads1115a.startSingleConvertion();
      adcTimer = 0;
      while(adcTimer < 1000) {}; //wait 1000 micros for read - Q ver of ADS1115
      valueADC = ads1115a.readConvertedValue();
      float mainVolts = valueADC / 100; // opAmp voltage divider x10 (actual voltage)
      //8.32 = 100%
      //6.8 = 0%


    // ----------------------------------  Check Haz Voltage  ------------------------
    
      int h = analogRead(pin_hazVolts);
      //.   >150 is on
      
     // float hazVolts = valueADC / 100; // opAmp voltage divider x10

      delay(10000);

      Serial.print("Main Voltage = ");
      Serial.println(mainVolts);
      Serial.print("Raw Read = ");
      Serial.println(valueADC);
      Serial.print("Haz Raw/Voltage = ");
      Serial.println(h);


}


void toggle5v() {
  Serial.print("5v External Toggle is now ");
  if(digitalRead(pin_ext5v)) {
    Serial.println("OFF");
    digitalWrite(pin_ext5v, LOW);
  } else {
    Serial.println("ON");
    digitalWrite(pin_ext5v, HIGH);
  }
 
}

void toggle6v() {
  Serial.print("6v External Toggle is now ");
  if(digitalRead(pin_ext6v)) {
    Serial.println("OFF");
    digitalWrite(pin_ext6v, LOW);
  } else {
    Serial.println("ON");
    digitalWrite(pin_ext6v, HIGH);
  }
 
}



void toggleFan() {
  Serial.print("Fan Toggle is now ");
  if(digitalRead(pin_fan)) {
    Serial.println("OFF");
    digitalWrite(pin_fan, LOW);
  } else {
    Serial.println("ON");
    digitalWrite(pin_fan, HIGH);
  }
 
}

void fuseTest() {
      Serial.print("Fuse Detect Status:  ");
      // If voltage is not on then this will report incorrectly


      if(digitalRead(pin_fuseMain) == LOW) {
        Serial.println("Main Fuse Good/Closed");
      } else {
        Serial.println("Main Fuse Open/Bad");
        //zzz check the voltage 
      }


      
}

void checkCont() {
      Serial.print("Igniter Continuity = ");
      if(digitalRead(pin_igniterContinuity) == LOW) {
        Serial.println("Closed");
      } else {
        Serial.println("Open");
      }
}

void checkTemp(){
      float CPUtemp = 0.0;
      Serial.println("Checking CPU Temperature...");Serial.println(" ");
      Serial.print("CPU Temp (f) = ");
      CPUtemp  = (tempmonGetTemp() * 9.0f / 5.0f) + 32.0f;
      Serial.println(CPUtemp);
      
}


void toggleIgniter(){
  Serial.print("Igniter Toggle is now ");
  if(digitalRead(pin_igniterFIRE)) {
    Serial.println("OFF");
    digitalWrite(pin_igniterFIRE, LOW);
  } else {
    Serial.println("ON");
    digitalWrite(pin_igniterFIRE, HIGH);
  }
}





void I2Cscan() {

 byte error, address;
  int nDevices;
  Serial.println("Scanning I2C Bus...");
  Wire.begin();
  delay(1000);
  
  nDevices = 0;
  for(address = 1; address < 127; address++ )
  {
    // The i2c_scanner uses the return value of
    // the Write.endTransmisstion to see if
    // a device did acknowledge to the address.
    Wire.beginTransmission(address);
    error = Wire.endTransmission();
 
    if (error == 0)
    {
      Serial.print("I2C device found at address 0x");
      if (address<16)
        Serial.print("0");
      Serial.println(address,HEX);
 
      nDevices++;
    }
    else if (error==4)
    {
      Serial.print("Unknown error at address 0x");
      if (address<16)
        Serial.print("0");
      Serial.println(address,HEX);
    }    
  }
  if (nDevices == 0)
    Serial.println("No I2C devices found\n");
  else
    Serial.println("done\n");
  Wire.end(); 

  
}

//*****************************************************************************  ADC STUFF ******************************

void PTloop() {

  // ADS1115 
  Wire.begin();
  delay(1);
  ads1115a.reset();
  delay(100);
  ads1115a.setDeviceMode(ADS1115_MODE_SINGLE);
  ads1115a.setDataRate(ADS1115_DR_860_SPS);
  ads1115a.setPga(ADS1115_PGA_6_144);
  delay(100); 
  Wire.setClock(400000); 
  delay(100);  

  uint16_t valueA = 0;
  uint16_t valueB = 0;

  float value0f = 0.0;
  float value1f = 0.0;
  float value2f = 0.0;
  float value3f = 0.0;



  unsigned long aMicros = 900;
  //int aMicros = 100000;
  unsigned long  bMicros = 900;
  int aRotate = 0;

  int aCounter[5] = {0,0,0,0};

  aRotate = nextA(aRotate);


  // Do the first one A
  if(aRotate == 1) ads1115a.setMultiplexer(ADS1115_MUX_AIN0_GND);
  if(aRotate == 2) ads1115a.setMultiplexer(ADS1115_MUX_AIN1_GND);
  if(aRotate == 3) ads1115a.setMultiplexer(ADS1115_MUX_AIN2_GND);
  if(aRotate == 4) ads1115a.setMultiplexer(ADS1115_MUX_AIN3_GND);
  ads1115a.startSingleConvertion();



  elapsedMillis timeIt = 0;
  elapsedMicros aTimer = 0;


  Serial.println("Starting Five Second Sampling Test...");
  Serial.println("    ");
  
  
  while(timeIt < 5000) {

    if(aTimer >= aMicros) {
      //Serial.print("Starting    ");
      valueA = ads1115a.readConvertedValue();
      //Serial.print(valueA);
      //Serial.print("   ");
      //Serial.print(aRotate);
      //Serial.print("   ");      
      if(aRotate == 1) value0f += (float) valueA;
      if(aRotate == 2) value1f += (float) valueA;
      if(aRotate == 3) value2f += (float) valueA;
      if(aRotate == 4) value3f += (float) valueA;
      aCounter[aRotate]++;
      //Serial.print(aCounter[aRotate]);
      //Serial.print("    Next:");
      aRotate = nextA(aRotate);
      //Serial.print(aRotate);
      //Serial.print("   ");
      if(aRotate == 1) ads1115a.setMultiplexer(ADS1115_MUX_AIN0_GND);
      if(aRotate == 2) ads1115a.setMultiplexer(ADS1115_MUX_AIN1_GND);
      if(aRotate == 3) ads1115a.setMultiplexer(ADS1115_MUX_AIN2_GND);
      if(aRotate == 4) ads1115a.setMultiplexer(ADS1115_MUX_AIN3_GND);
      ads1115a.startSingleConvertion();
      aTimer = 0;
      //Serial.println("DONE!   ");
    }

    
  } // end five second while





  Serial.println("ACD1 Values:     ");
  if(aEnabled[0] == 1) value0f = value0f / (float) aCounter[1];
  if(aEnabled[1] == 1) value1f = value1f / (float) aCounter[2];
  if(aEnabled[2] == 1) value2f = value2f / (float) aCounter[3];
  if(aEnabled[3] == 1) value3f = value3f / (float) aCounter[4];
  
  Serial.print(" (VOL) IN 0: ");
  Serial.print(value0f,0);
  Serial.print("     count: ");
  Serial.println(aCounter[1]);
  Serial.print(" (HAZ) IN 1: ");
  Serial.print(value1f,0);
  Serial.print("     count: ");
  Serial.println(aCounter[2]);
  Serial.print(" (N/A) IN 2: ");
  Serial.print(value2f,0);
  Serial.print("     count: ");
  Serial.println(aCounter[3]);
  Serial.print(" (PSP) IN 3: ");
  Serial.print(value3f,0);
  Serial.print("     count: ");
  Serial.println(aCounter[4]);
  Serial.println("  ");

 

}



int nextA(int curVal) {
 int iNext = curVal +1;
 if(iNext > 4) iNext = 1;
 int iNext2 = 0;
 for(int i=0;i < 4;i++) {
  iNext2 = iNext++;
  if(iNext2 == 5) iNext2 = 1;
  if(aEnabled[iNext2-1] == 1) return iNext2;
 }
 return 0; // nothing enabled
}








void toggleLB() {
  Serial.print("LED Built-in Toggle is now ");
  if(digitalRead(pin_internalLED)) {
    Serial.println("OFF");
    digitalWrite(pin_internalLED, LOW);
  } else {
    Serial.println("ON");
    digitalWrite(pin_internalLED, HIGH);
  }
 
}

void toggleLed1() {
  Serial.print("LED1 Toggle is now ");
  if(digitalRead(pin_led1)) {
    Serial.println("OFF");
    digitalWrite(pin_led1, LOW);
  } else {
    Serial.println("ON");
    digitalWrite(pin_led1, HIGH);
  }
 
}

void toggleLed2() {
  Serial.print("LED2 Toggle is now ");
  if(digitalRead(pin_led2)) {
    Serial.println("OFF");
    digitalWrite(pin_led2, LOW);
  } else {
    Serial.println("ON");
    digitalWrite(pin_led2, HIGH);
  }
 
}


void toggleBuzzer() {
  Serial.print("Buzzer Toggle is now ");
  if(digitalRead(pin_buzzer)) {
    Serial.println("OFF");
    digitalWrite(pin_buzzer, LOW);
  } else {
    Serial.println("ON");
    digitalWrite(pin_buzzer, HIGH);
  }
}


void continuitySwitch() {
  Serial.print("Continuity switch is ");
  if(digitalRead(pin_continuitySwitch) == HIGH) {
    Serial.println("OPEN  (not pressed)");
  } else {
    Serial.println("CLOSED  (pressed)");
  }
}


void rocketConnect() {
  

  Serial.print("The Rocket umbilical is  ");
  if(digitalRead(pin_rocketDetect) == HIGH) {
    Serial.println("NOT CONNECTED  (open)");
  } else {
    Serial.println("CONNECTED  (closed)");
  }
}


//***************************************************  RADIO STUFF ********************************************


void RadioTXtest(){

    Serial.println("Initiating Radio Transmit Test...");
    Serial.println(" ");
    Serial1.begin(19200);
    Serial.println("Transmitting 10 packets....");
    for(int i=0; i < 10; i++) {
      Serial1.print("@M,33,Hello World hello hello hello hello hello hello hello hello hello hello hello hello hello hello hello ,!");
    }
    Serial.println("Done.");

}


void radioTest() {
  
    Serial.println("Initiating Radio Test...");
    Serial.println(" ");
    digitalWrite(pin_radioSet, HIGH); //turn radio set pin to low
    delay(50);
    Serial1.begin(9600);
    char s[5];
    strcpy(s,"");
    unsigned long testtime = millis() + 3500;
    s[0] = 0xaa;
    s[1] = 0xfa;
    s[2] = 0xaa; // aa = product model number 
    s[3] = 0x0d; //  /r termination
    s[4] = 0x0a; //  /n termination
    Serial1.println(s);
    int x = 0;
    while(x < 1) {
      checkRadio();
      if(newWord == 1) {
        Serial.print("Radio Rx:  ");
        Serial.println(theWord);
        char *ptr = strstr(theWord, "LORA6100");
        if (ptr != NULL) Serial.println("Radio Set Comms Test Successful!"); 
        digitalWrite(pin_radioSet, LOW); //turn radio set pin to low
        delay(2000);
        Serial1.begin(19200);
        Serial1.print("@M,33,Hello World,!");
        Serial1.flush();
        Serial.println(" "); 
        Serial.println("Message Sent"); 
        
        x = 1;
        
      }
      if(millis() > testtime) {
        Serial.println("Radio Timeout");
        digitalWrite(pin_radioSet, LOW); //turn radio set pin to low
        delay(200);
        Serial1.begin(19200);
        x = 2;
      }
       
    }
}
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

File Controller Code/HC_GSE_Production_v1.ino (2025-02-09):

/*   ***********  HALF CAT OPEN GSE Controller - 2024-2025 by Mike and Preston Brinker  ***********
 * 
    Pressure Transducer CODES:
    • PTK = Pressure Tank
    • PCH = Pressure Chamber
    • PLD = Pressure Load

    Valves:
    • SOX = Servo OX
    • SFU = Servo Fuel
    • SFL = Servo Fill
    • SPG = Servo Purge
 *     
 *   
 */


  bool serialDebug = false;  // set to true to get Serial output for debugging (compile 396Mhz!)
  bool debugMode = false;
  bool mute = true;  // silence the buzzer for testing

 // Pin configuration
  #define RXD1 0
  #define TXD1 1
  #define RXD2 7
  #define TXD2 8
  #define pin_rocketDetect 16 // PU 
  #define pin_igniterContinuity 33 
  #define pin_continuitySwitch 31 // PU
  #define pin_led1 28 //
  #define pin_led2 29 //
  #define pin_buzzer 30 //
  #define pin_igniterFIRE 34 // 
  #define pin_SFL 22 
  #define pin_SPG 23
  #define pin_SFU 15
  #define pin_SOX 14
  #define pin_servoSpare 36
  #define pin_hazVolts A11
  #define pin_radioSet 27
  #define pin_internalLED 13
  #define pin_ext5v 35
  #define pin_ext6v 21
  #define pin_fuseMain 20
  #define pin_fan 26
  #define pin_analogSpare A14
  #define pin_digSpare 39

//Teensy
  #include "Arduino.h"
  extern "C" uint32_t set_arm_clock(uint32_t frequency); // required to set MCU clock speed


//INA219 -- current and voltage sensing add
  #include <Wire.h>
  #include <Adafruit_INA219.h>
  Adafruit_INA219 ina219;

 //Servos
  #include <Servo.h> 
  Servo SFU;  
  Servo SOX;
  Servo SFL;
  Servo SPG;

  struct configStruct {  // master configuration
     // PT ranges - assume all are .5v-4.5v 
     byte PTKenabled = 1;
     int PTKrange = 500;
     float PTKzero = .5;
     int PTKalarm = 425;
     byte PCHenabled = 1;
     int PCHrange = 500;
     float PCHzero = .50;
     byte PLDenabled = 1;
     // Servos
     int SFUopen = 500;
     int SFUclose = 1200;
     int SOXopen = 500;
     int SOXclose = 1200;
     int SFLopen = 500;
     int SFLclose = 1200;
     int SPGopen = 500;
     int SPGclose = 1200;

     int pressureWaitTime = 2000; //only send changes every 2 seconds
     int pressureMinChange = 4;
      
     int CPUtempAlarm = 165;
     int DAQauto = 1;
     int DAQtimeout = 50000;
     
             
  };
  configStruct configuration;

  struct localStruct {
    // used for local code configuration / non-configurable
    int battlow = 15;
    int logRate = 10; // 100 hz (10ms pause)
    int DAQsuperTimeout = 180000; // three minutes super timeout
    int DAQflush = 10000; // millis to safety close/open/flush file
    int FTPsize = 100; // FTP packet size - increase sendChunk below
    bool radioLog = true; // local config to enable radio logging
    int ADCint = 6; // interval for reading ADC units in millis 6=115sps ZZZ
    unsigned long mvInt = 500; // interval to read main volts in ADC
    unsigned long hzInt = 500; // interval to read haz volts from ADC
    elapsedMillis hzTimer = 0;
    elapsedMillis mvTimer = 0;
    unsigned long ADCwait = 2000; // microseconds to wait for ADC to sample
    int servo6vhold = 2000; //turn on servo power for 2 seconds when moving them
   
  };
  localStruct local;


  struct timerStruct {  // timer variables
    unsigned long radioRXTimer = 0;
    unsigned long radioTXTimer = 0;
    unsigned long radioSendCallSignTimer = 90000;
    unsigned long healthTimer = 0;
    unsigned long healthResend = 0;
    int radioRXInterval = 300;
    int radioTXInterval = 1000;
    int radioSendCallSignInterval = 90000;
    unsigned long housekeepingInput = 0;
    int housekeepingInputInterval = 500;  // set to 500 ms for now
    unsigned long fullStatusTimer = 0;
    int fullStatusInterval = 10000; // send full status every 10 seconds (and when an event)
    unsigned long pressureTimer = 0;
    unsigned long igniterTimer = 0;
    unsigned long LineTimer = 0;
    unsigned long QDoff = 0;
    unsigned long oxLineTimer = 0;
    unsigned long mainOff = 0;
    unsigned long mainOn = 0;
    unsigned long health = 0; // error check
    elapsedMillis errorBlink = 0;
    unsigned long timer6v = 0; 
    elapsedMillis processPF60 = 0;
    elapsedMillis processPurge = 0;
    elapsedMillis servoTimer = 0;
  };
  timerStruct timers;

  struct workingStruct {  // working variables

    char statusSentenceString[200]; // full status to send
    char configString[200]; // full config send
    int lastPTK = 0;
    int lastPCH = 0;
    int lastPLD = 0;
    bool PTKzero = false;
    bool PCHzero = false;
    bool PLDzero = false;

    // DAQ, Logging, and File TX and Flash
    byte DAQstart = 0; // 1 = start, 2 = stop
    byte DAQrecording = 0;
    byte DAQstudent = 1;
    char DAQfilename[20];
    char rLogFilename[20];
    int flashFormat = 0;
    char code[6];
    int confvalue;
    int radioLog = 0;
    char radioLogString[200];
    //FTP send controls
    volatile bool requestDir = false;
    int dirFileCount = 0;
    int totalPackets = 0;
    volatile bool sendFlag = false;
    char sendFile[20];
    char sendChunk[110];
    int currentPacket = 0;
    bool ftpMode = false;
    bool getFile = false;
    elapsedMillis superTimeout = 0;  
    bool beepErrors = false; // for first health check beeping
    int logCache = 0; //cache radio inbound during DAQ 
    char logCacheStr[25][200];
    bool writeConfig = false;
    bool SDcopy = false;
    bool SD = false; // is there a valid SD card?
    unsigned long fillTime = 60;
    unsigned long purgeTime = 10;
    bool radioOff = false;
    bool servoTest = false;

  };
  workingStruct working;

  struct errorsStruct {

    int mainBatt = 2;
    int MCUtemp = 2;
    int PT = 2;
    int radio = 2;
    int flashMem = 2;
    int SD = 2;
    int ADC = 2;
    int MCUcrash = 2;
    int errorCount = 0;
    int fuse5v = 2;
    int fuseMain = 2;
  };
  errorsStruct errors;

  struct padStatusStruct {

    //new PT values 
    int PTK = 0;  // Tank
    int PLD = 0;  // Load
    int PCH = 0;  // Chamber
    byte rocketConnected = 0;
    byte padHot = 0; //pad safety plug in/out (haz 24v) 
    byte armedState = 0;
    byte igniterContinuity = 0;
    int mainVolts = 0;
    byte SOX = 0; //closed = 0, open = 1
    byte SFU = 0;
    byte SFL = 0;
    byte SPG = 0;
    byte processFill60 = 0; // can be 0- not run, 1 - complete, 2 - running, 3-stopped
    byte processPurge = 0;
    byte processLaunch = 0;
    byte processAbort = 0;
    int CPUtemp = 0;


  };
  padStatusStruct padStatus;


// *** Radio Setup
  char radioHeader[7];
  char radioMessage[150];
  char radioMessageS[200];
  int newWord = 0;
  char theWord[320];
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
